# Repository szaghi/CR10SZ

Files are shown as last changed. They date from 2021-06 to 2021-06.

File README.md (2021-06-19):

### CR10SZ, a modified CR10S 3D printer (aka cariola 2.0)

Creality CR10S is a decent 3D printer with large volume, but to obtain good quality the printing speed must be kept very low. Moreover, its usage is not straightforward, in particular for newbies (my CR10S is going to be a present for a friend of mine without any 3D printing experience). As a consequence, I modify my CR10S in order to improve speed printing (maintaining good quality) and easyness of usage.

The modifications involve both mechanics and electronics.

#### Mechanics mods

The (brief) list of mechanics mods is:

+ adopt linear rails (MGN12H) for both X and Y axis (more precise at high speed than stock wheels carriages);
+ move the 2 Z steppers to the top from the bottom in order to allow T8 screws (that are not of good quality) to work *in traction* and not *in compression*;
+ add Z frame braces to increase frame rigidity;
+ change extruder configuration from bowden to direct: a BMG (clone) extruder has been configured in direct mode over a microswiss (original) hotend; the X carriage has been designed from scratch and it allows the usage of a 5015 blower with a good-flow, short, fan duct within a very accurate inductive Z-probe for automatic bed leveling a Z-tilt-adjust.

#### Electronics mods

The (brief) list of electronics mods is:

+ use SKR 1.4 turbo mainboard with TMC 2209 drivers: in particular 2 independent drivers are used for the 2 Z axis thus, coupling the usage of Z-probe, to perform Z-tilt-adjust;
+ use BTT TFT35-E3-V3.0 display to control the printer;
+ use raspberry Pi 3 b+ to control the board by means of Klipper firmware;
+ use Wantai 42BYGHM810 Nema 17 steppers for X and Y axis, while use Stepperonline 17HS19-2004S1 Nema 17 for the 2 Z axis; the direct extruder is moved by Stepperonline 17HS08-1004S3 Nema 17 panckage stepper.

#### Overview of the final result

Combining all mods, the new CR10S (CR10SZ aka cariola 2.0) results as a standalone (no more separated control box with flying cables) 3D printer with a *Klipperized* heart that provides great quality even at high speed for this kind of kinematics and building volume and also allowing an easy web control by means of Fluidd interface.

#### Files

Many mods are taken from thingiverse and their STL are included here only for the sake of simplicity, but all rights and merits must go to their authors. Others mods as been designed from scratch: a Blender file is provided including all mods, use the blend file instead of STL if in doubt.

+ `blend/CR10SZ.blend` contains all mods, refer to it also for the assembly;
+ mods taken from thingiverse:
   + SKR mount https://www.thingiverse.com/thing:4047923

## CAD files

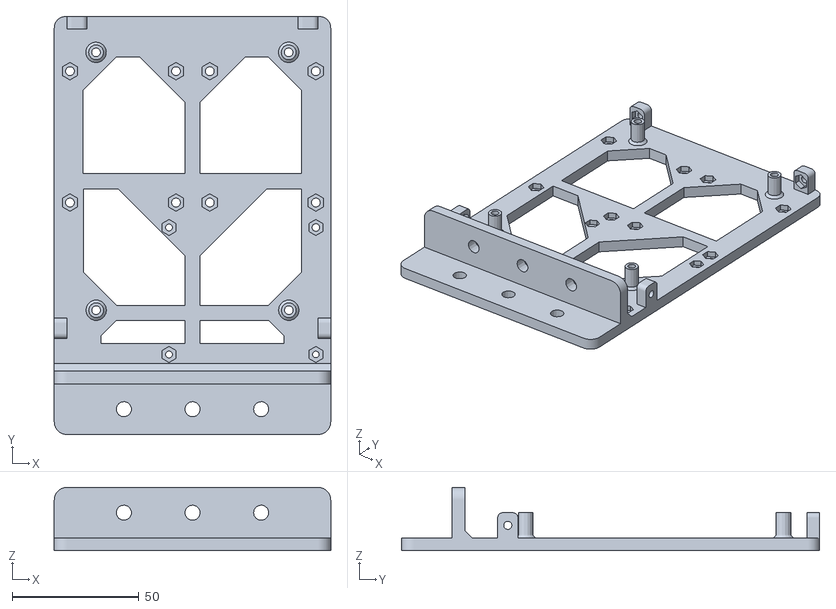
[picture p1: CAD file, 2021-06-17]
stl/CR-10S-SKR-mount.stl
109.2 x 165.2 x 25.0

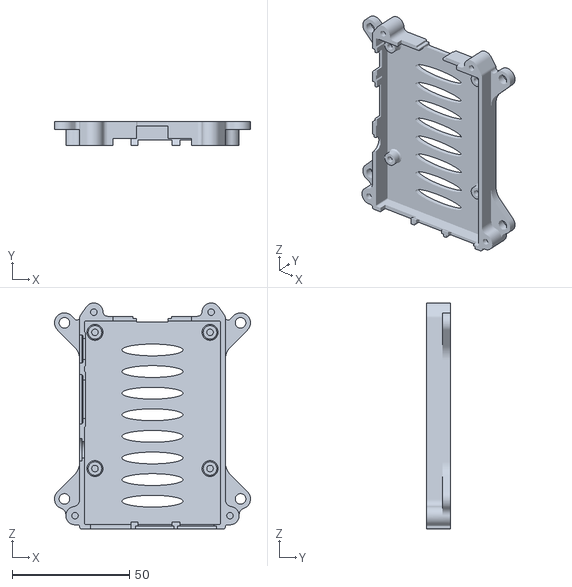
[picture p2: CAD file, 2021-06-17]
stl/CR-10S-raspberry-bottom.stl
83.5 x 10.3 x 96.2

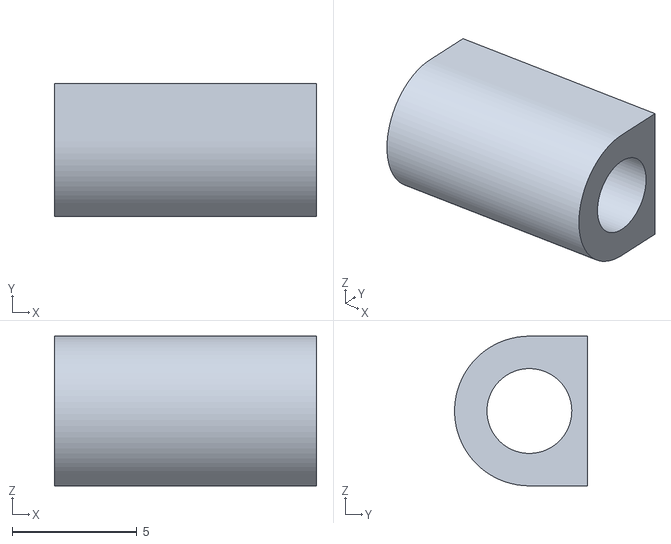
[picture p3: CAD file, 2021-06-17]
stl/CR-10S-SKR-TFT-Stand-off-bottom-LR-V1.stl
10.5 x 5.32 x 6.00

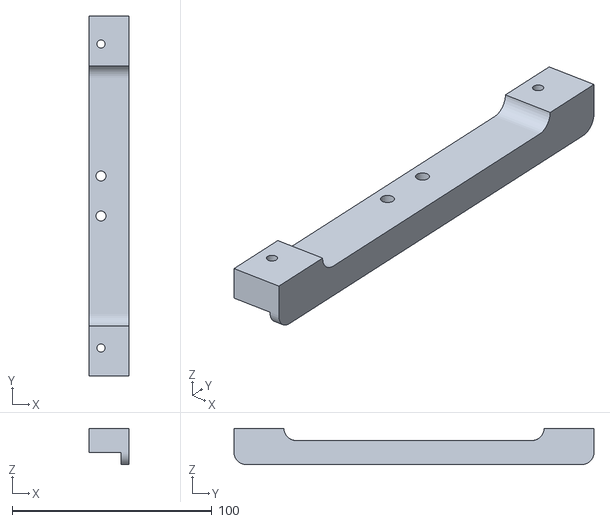
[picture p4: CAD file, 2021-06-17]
stl/CR-10S-Y-bed-reinforce.stl
20.0 x 180.0 x 18.0

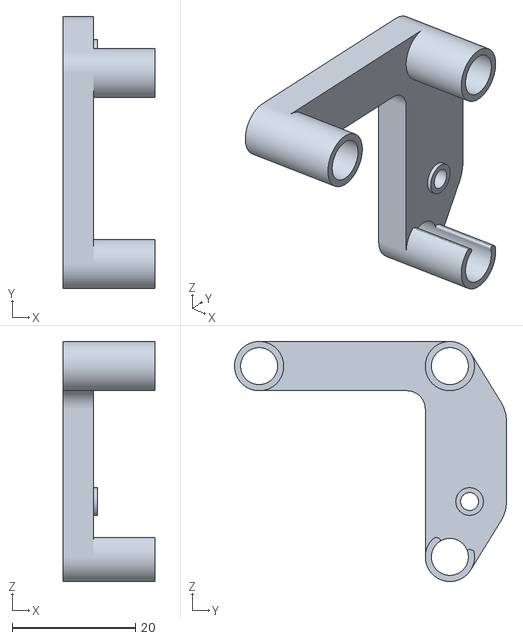
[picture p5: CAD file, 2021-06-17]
stl/CR-10S-X-tensioner-left-back-frame_.stl
15.0 x 44.2 x 39.0

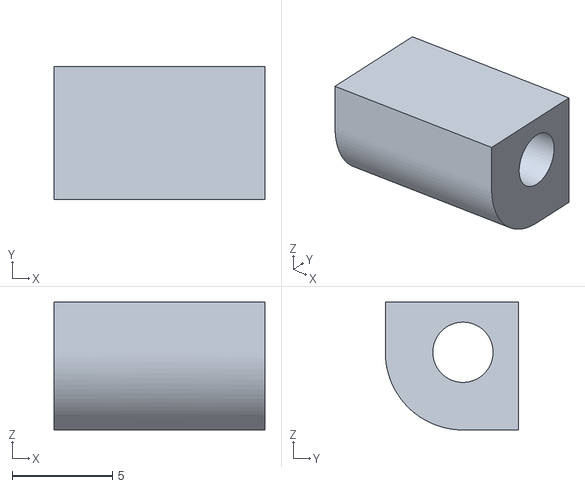
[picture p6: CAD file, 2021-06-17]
stl/CR-10S-SKR-TFT-Stand-off-top-left-V1.stl
10.5 x 6.64 x 6.37

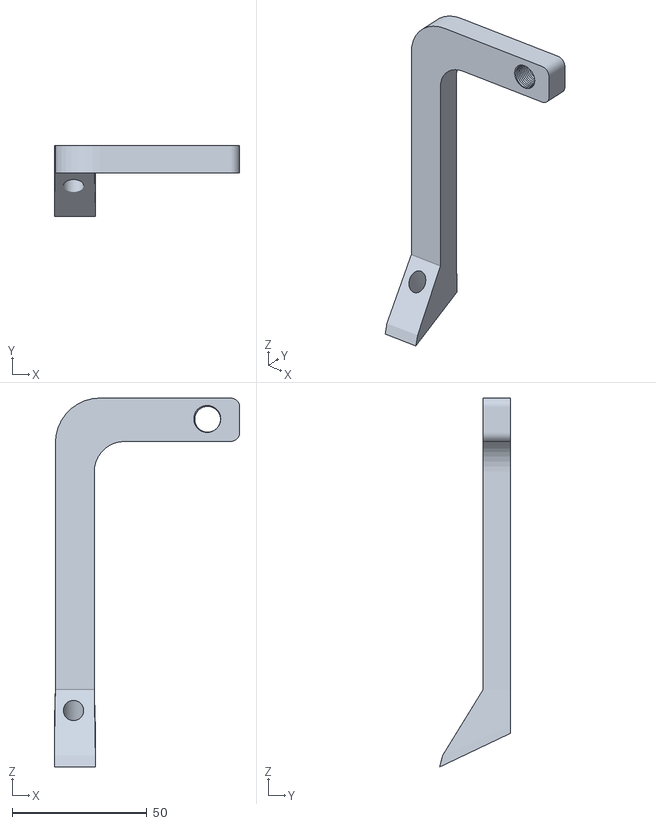
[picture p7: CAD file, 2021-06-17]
stl/CR-10S-Y-spool-feeder.stl
68.9 x 26.3 x 137.0

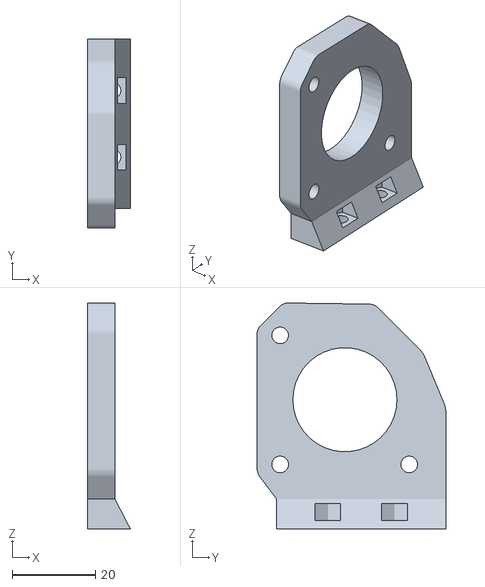
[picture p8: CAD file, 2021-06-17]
stl/CR-10S-X-carriage-plate-bmg.stl
10.3 x 45.4 x 54.3

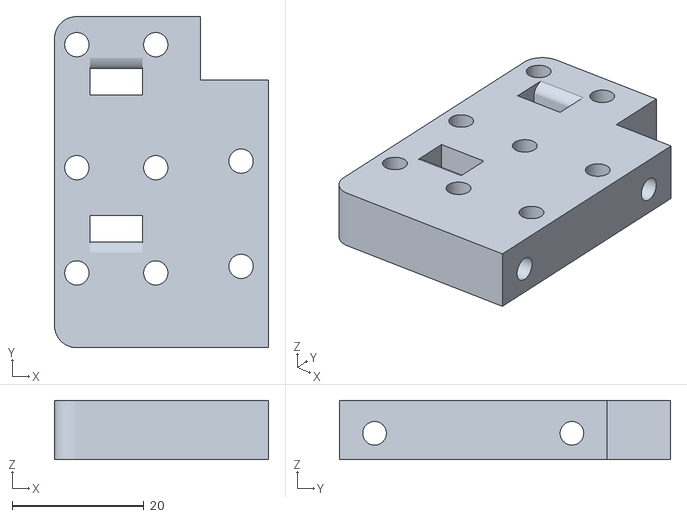
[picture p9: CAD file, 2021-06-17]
stl/CR-10S-X-carriage-plate-top.stl
32.5 x 50.3 x 9.00

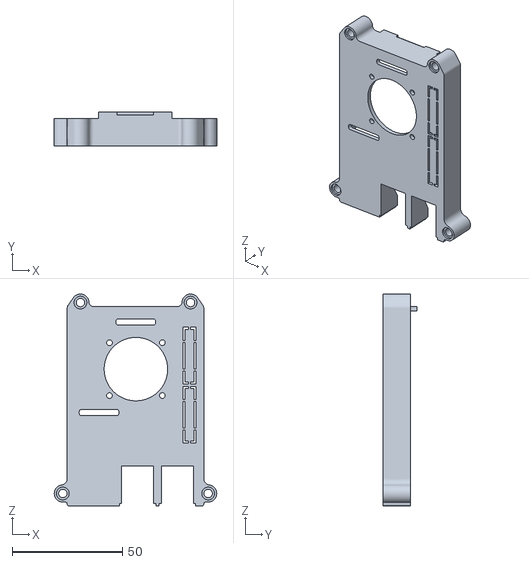
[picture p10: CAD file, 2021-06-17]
stl/CR-10S-raspberry-top.stl
73.8 x 15.5 x 96.2

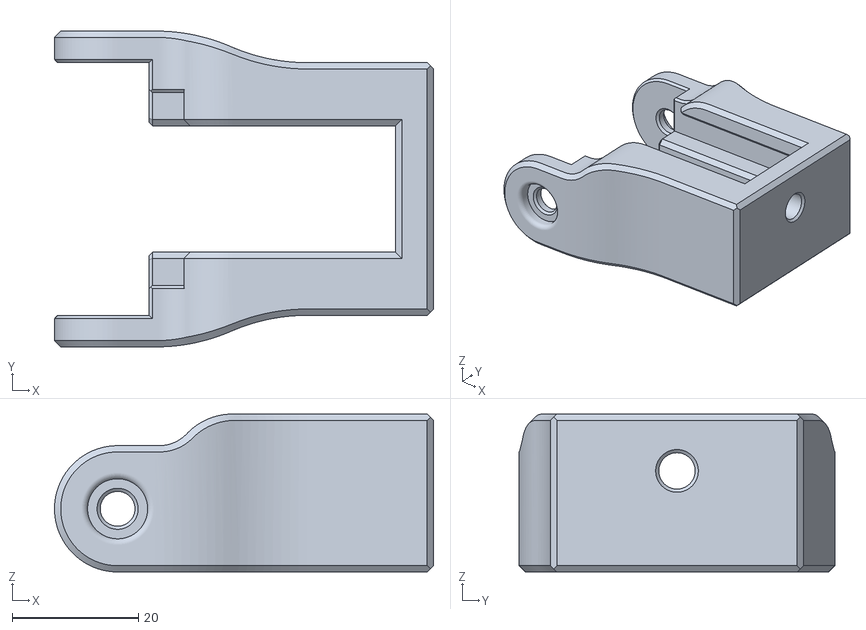
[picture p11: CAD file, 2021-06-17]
stl/CR-10S-Y-tensioner-bracket.stl
60.0 x 50.0 x 25.0

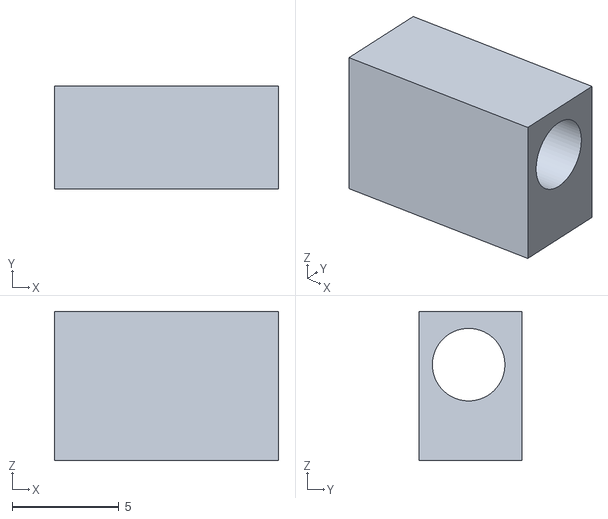
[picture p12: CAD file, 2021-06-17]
stl/CR-10S-SKR-TFT-Stand-off-top-right-V1.stl
10.5 x 4.82 x 7.00

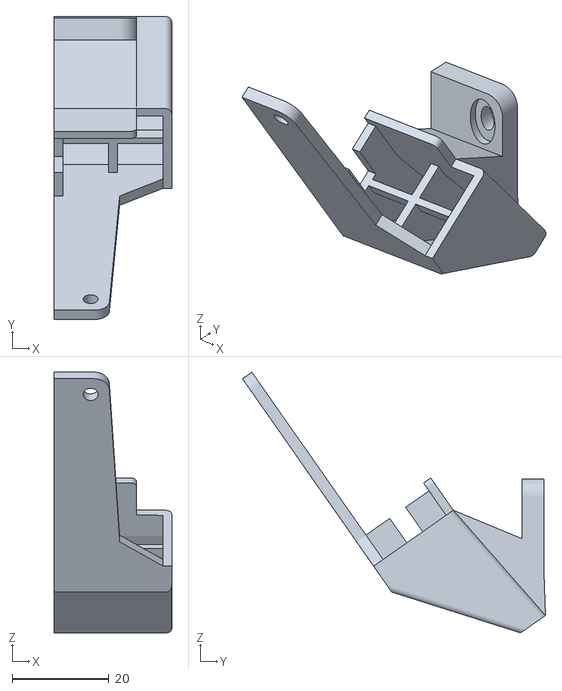
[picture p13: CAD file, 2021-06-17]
stl/CR-10S-X-carriage-5015-fan-duct.stl
24.3 x 62.7 x 53.9

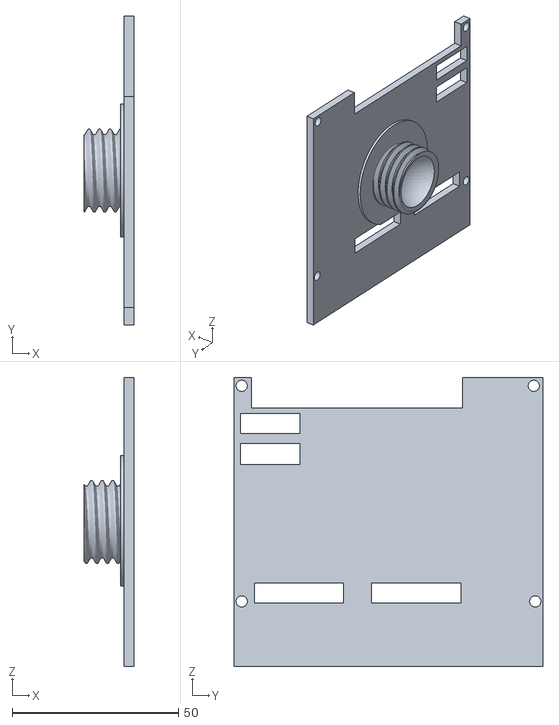
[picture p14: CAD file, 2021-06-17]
stl/CR-10S-SKR-TFT--Back-V1.stl
15.0 x 93.0 x 87.0

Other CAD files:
cura-profile/CR10SZ-cura_profile.3mf
stl/CR-10S-SKR-TFT-Ball-V1.stl
stl/CR-10S-SKR-TFT-locknut-V1.stl
stl/CR-10S-X-carriage-inductive-sensor-mount.stl
stl/CR-10S-SKR-120mm-holder.stl
stl/CR-10S-SKR-TFT-Exstrusion_-V1.stl
stl/CR-10S-SKR-TFT-Front-V1.stl
stl/CR-10S-X-carriage-plate-front.stl
stl/CR-10S-X-carriage-plate-top-belt-holder.stl
stl/CR-10S-X-tensioner-left-front-frame_.stl
stl/CR-10S-Y-MGN12H-support.stl
stl/CR-10S-Y-spool-holder.stl
stl/CR-10S-Y-tensioner-sled-ext.stl
stl/CR-10S-Z-frame-brace-bottom.stl
stl/CR-10S-Z-frame-brace-top.stl
stl/CR-10S-Z-motor-top-bracket.stl
stl/CR-10S-squash-foot_001.stl

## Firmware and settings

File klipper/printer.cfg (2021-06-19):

[include kiauh_macros.cfg]

[mcu]
serial: /dev/serial/by-id/usb-Klipper_lpc1769_1330010BA39869AFAC4C405EC42000F5-if00

[pause_resume]

[display_status]

[virtual_sdcard]
path: ~/gcode_files

[printer]
kinematics: cartesian
max_velocity: 300           ; mm/s
max_accel: 3000             ; mm/s2
max_accel_to_decel: 2000    ; mm/s2
max_z_velocity: 15          ; mm/s
max_z_accel: 200            ; mm/s2
square_corner_velocity: 5.0 ; mm/s

[input_shaper]
shaper_freq_x: 37.8
shaper_freq_y: 39.1
shaper_type: mzv

[skew_correction]
[skew_correction skew_profile]
xy_skew = -0.00568192966364
xz_skew = 0.0
yz_skew = 0.0

# steppers

[stepper_x]
step_pin: P2.2
dir_pin: P2.6
enable_pin: !P2.1
microsteps: 16
full_steps_per_rotation: 400
rotation_distance: 40 # 400*16/160
endstop_pin: P1.29
position_endstop: -5
position_min: -5
position_max: 310
homing_speed: 80

[tmc2209 stepper_x]
uart_pin: P1.10
run_current: 1.700
hold_current: 1.300
interpolate = True
stealthchop_threshold: 0

[stepper_y]
step_pin: P0.19
dir_pin: !P0.20
enable_pin: !P2.8
microsteps: 16
full_steps_per_rotation: 400
rotation_distance: 40 # 400*16/160
endstop_pin: P1.28
position_endstop: 0
position_max: 315
homing_speed: 50

[tmc2209 stepper_y]
uart_pin: P1.9
run_current: 1.500
hold_current: 1.000
interpolate = True
stealthchop_threshold: 0

[stepper_z]
step_pin: P0.22
dir_pin: !P2.11
enable_pin: !P0.21
microsteps: 16
rotation_distance: 8 # 200*16/400
endstop_pin: probe: z_virtual_endstop 
#endstop_pin: P1.27
#position_endstop: 0.0
position_min: -2
position_max: 360

[tmc2209 stepper_z]
uart_pin: P1.8
run_current: 1.600
hold_current: 1.200
interpolate = True
stealthchop_threshold: 0

#[extruder1]
#heater_pin: P2.4
#sensor_pin: P0.23
[stepper_z1]
step_pin: P1.15
dir_pin: !P1.14
enable_pin: !P1.16
microsteps: 16
rotation_distance: 8 # 200*16/400
#endstop_pin: probe: z_virtual_endstop 
#position_max: 360

#[tmc2209 extruder1]
[tmc2209 stepper_z1]
uart_pin: P1.1
run_current: 1.600
hold_current: 1.200
interpolate = True
stealthchop_threshold: 0

# Z settings

[probe]
pin: !P1.27
x_offset: 34.865
y_offset: 30.7
z_offset: 0.75
samples: 3

#[safe_z_home]
#home_xy_position: 155,155
#speed: 50.0
#z_hop: 10

[homing_override]
axes: z
set_position_z: 0
gcode:
   G91
   G1 Z10 F600
   G28 X Y
   G1 X155 Y155 F3600
   G28 Z
   G90

[z_tilt]
z_positions:
   0,150
   310,150
points:
   5,180
   255,180
speed: 50
horizontal_move_z: 5

[bed_mesh]
speed = 120
horizontal_move_z = 10
mesh_min = 35,71 # 0+35,40+31
mesh_max = 275,331 # 240+35, 300+31
probe_count = 3,3
fade_start = 1.0
fade_end = 10.0

# extruder & bed

[extruder]
step_pin: P2.13
dir_pin: !P0.11
enable_pin: !P2.12
microsteps: 16
rotation_distance: 7.800
nozzle_diameter: 0.400
filament_diameter: 1.750
heater_pin: P2.7
sensor_type = ATC Semitec 104GT-2
sensor_pin: P0.24
control = pid
pid_kp = 29.055
pid_ki = 1.266
pid_kd = 166.705
min_extrude_temp: 180
min_temp: 0
max_temp: 300
max_extrude_only_distance: 999999.0
pressure_advance: 0.1

[tmc2209 extruder]
uart_pin: P1.4
run_current: 0.800
hold_current: 0.500
stealthchop_threshold: 0

[heater_bed]
heater_pin: P2.5
sensor_type: EPCOS 100K B57560G104F
sensor_pin: P0.25
control = pid
pid_kp = 72.775
pid_ki = 0.919
pid_kd = 1440.939
min_temp: 0
max_temp: 130

# fans

[fan]
pin: P2.3
kick_start_time: 0.300

[heater_fan extruder_fan]
pin: P2.4
heater: extruder
heater_temp: 45.0
fan_speed: 1.0

# macros

[gcode_macro BED_LEVELING]
gcode:
   G28
   BED_MESH_CLEAR
   #Z_TILT_ADJUST
   BED_MESH_CALIBRATE
   BED_MESH_PROFILE SAVE=bed_mesh.dat
   BED_MESH_PROFILE LOAD=bed_mesh.dat


[gcode_macro START_SCRIPT]
gcode:
   {% set BED_TEMP = params.BED_TEMP|default(60)|float %}
   {% set EXTRUDER_TEMP = params.EXTRUDER_TEMP|default(190)|float %}
   M140 S{BED_TEMP}      ; start bed heating
   G90                   ; use absolute coordinates
   G28                   ; home the printer
   M190 S{BED_TEMP}      ; wait for bed to reach temperature
   M109 S{EXTRUDER_TEMP} ; set and wait for nozzle to reach temperature
   SKEW_PROFILE LOAD=skew_profile
   BED_MESH_PROFILE LOAD=bed_mesh.dat
   PURGE_LINE_LEFT

[gcode_macro END_SCRIPT]                                                                     
gcode:
   G28 Y
   TURN_OFF_HEATERS
   M106 S0   ; turn-off fan
   M84 X Y E ; disable all steppers but Z

[gcode_macro PURGE_LINE_LEFT]
gcode:
   G92 E0                          ; reset extruder
   G1 X0.2 Y20 Z0.2 F5000.0        ; move to start position
   G1 X0.2 Y200.0 Z0.2 F1500.0 E15 ; draw the first line
   G1 X0.5 Y200.0 Z0.2 F5000.0     ; dove to side a little
   G1 X0.5 Y20 Z0.2 F1500.0 E30    ; draw the second line
   ; G1 E-4 F1000                    ; retract a bit
   G92 E0                          ; reset extruder

[gcode_macro SAFE_HOME_X]
gcode:
   G91               ; relative positionning
   G1 E-2 F1000      ; retract a bit
   G1 E-2 Z0.2 F1000 ; retract and raise Z
   G1 X5 Y5 F3000    ; wipe out
   G1 Z10            ; raise Z more
   G28 X             ; home X axis

# menu custom
[menu __main __custom]
type: list
name: Custom

[menu __main __custom __bedleveling]
type= command
name= bed leveling
gcode:
   BED_LEVELING

[menu __main __custom __ZtiltAdjust]
type= command
name= Zetas Tilt Adjust
gcode:
   G28
   Z_TILT_ADJUST

# pins

[board_pins]
aliases: 
	EXP1_1=P1.30, EXP1_3=P1.18, EXP1_5=P1.20, EXP1_7=P1.22, EXP1_9=<GND>,
	EXP1_2=P0.28, EXP1_4=P1.19, EXP1_6=P1.21, EXP1_8=P1.23, EXP1_10=<5V>,
	EXP2_1=P0.17, EXP2_3=P3.26, EXP2_5=P3.25, EXP2_7=P1.31, EXP2_9=<GND>,
	EXP2_2=P0.15, EXP2_4=P0.16, EXP2_6=P0.18, EXP2_8=<RST>, EXP2_10=<NC>

[display]
lcd_type: emulated_st7920
spi_software_miso_pin: EXP1_6
spi_software_mosi_pin: EXP1_3
spi_software_sclk_pin: EXP1_5
en_pin: EXP1_4
encoder_pins: ^EXP2_3, ^EXP2_5
click_pin: ^!EXP1_2

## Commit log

2021-06-17 initialize repo
    [CR-10S-SKR-120mm-holder.stl, CR-10S-SKR-TFT--Back-V1.stl, CR-10S-SKR-TFT-Ball-V1.stl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]
2021-06-18 update cura profile
    [CR10SZ-cura_profile.3mf]
2021-06-19 minor updates
    [CR10SZ-cura_profile.3mf, printer.cfg]
